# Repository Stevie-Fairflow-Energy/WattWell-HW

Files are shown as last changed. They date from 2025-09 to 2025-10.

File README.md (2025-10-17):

# Aim of the project
WattWell - An inverter, built for a lifetime. 
A home inverter, to interface battery systems and PV systems with the UK and EU electricity grids.

The WattWell must be:
- Durable
- Repairable
- Open-Source

The main goal of the project is to develop an open source inverter (Hardware and Software).  
The initial configuration of the project will be a single phase, 5 kW inverter. 

An important part of the project is to be able to work with different types of switching components (IGBT/MOSFET). Nowadays, we often see that inverters are replaced after 10 years but they keep working or some faulty inverters that are not easily repared because the design is not modular or easy to fix.

Then, the goal is to design an Open Source inverter that is modular to be easy to be fixed and flexible enough to have differents functionalities (batteries/PV/...)

The project will be divided into different "workpackages" based on the functional blocks needed to make the whole system work. These functional blocks are called "Modules", and may be split into further modules where necessary. The diagram below shows the module definitions we are currently working to. 

WattWell Block Diagram-External Interfaces - Operational drawio (3)

1. Supervisory control: development of the main control board able to get the measurements, generate references, ... This board embeds the main mcu.
2. Inverter Board
3. DC/DC converter: Able to take a variable DC input (48V +/- 20%) and output a stable DC output controllable between 360 V and 500 V.
4. DC Link: A DC link capable of self-protection
5. A DC filter for smooth input/output
6. DC Protections for over-current and over-voltage protection
7. DC connections for physically connecting the DC source to WattWell
8.  AC filter for smooth sine wave input/output
9. AC protection for over-current and over-voltage protection. Required for compatibility with grid codes.
10. Connections for phsyically conecting the external electrical system to WattWell
11. Human Machine Interface (HMI) to act as the interface between the user and the supervisory control

For the Inverter board, two sub-modules are assumed:
1. Control and Driver board: interface between the supervisory control board and power switch (IGBT's/Mosfet's). The driver board needs to generate the PWM signals based on a reference from the supervisor.
2. Power circuit: power circuit of the inverter

# Expected functionalities

- Being able (and allowed) to be connected to the European grid
- MPPT for solar panels (with DC/DC)
- Battery connection
- Communication capabilities (serial,...)
- Working in islanding mode (offgrid)

# 1. Supervisory control board:

For the supervisory control, the firmware on the main mcu should have (main mcu based on STM32G434):

1. Low level drivers
2. Basics functionalities (bootloader, debug uart, pll,...)
3. Advanced functionalities (power management, MPPT, state machine)

The main control board will be able to measure:
1.  3AC voltages (max 400V) - ADC min 14bits
2.  2DC voltages (max 1500V) -ADC min 14bits
3.  4AC/DC current measurement - ADC min 14bits
4.  Temperature measurement

The main control board will have the following interface:
1.  2X UART(1X to RS485; 1X to USB)
2.  1xSPI
3.  2xI2C
4.  1xCAN
5.  6X PWM's
6.  6X DO's
7.  6X DI's
8.  6X AI'S (temp from IGBT/Mos)

Other functions:
1.  Debug LED
2.  RTC (supercap based)
3.  Additionnal ROM (TBD)
4.  Watchdog
5.  Power supply for IGBT's/Mosfets

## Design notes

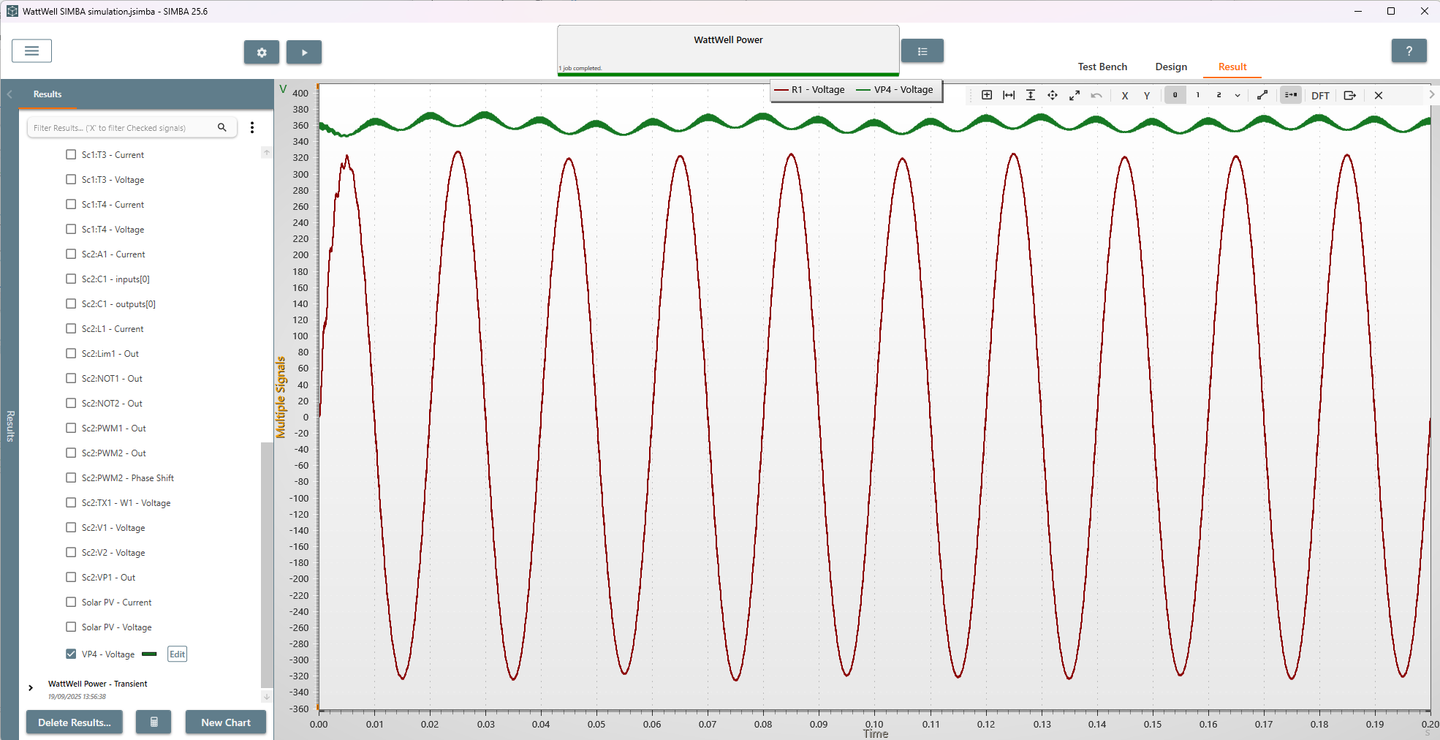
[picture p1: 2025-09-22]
WattWell-Simulations/Screenshots/Screenshot 2025-09-19 140105.png

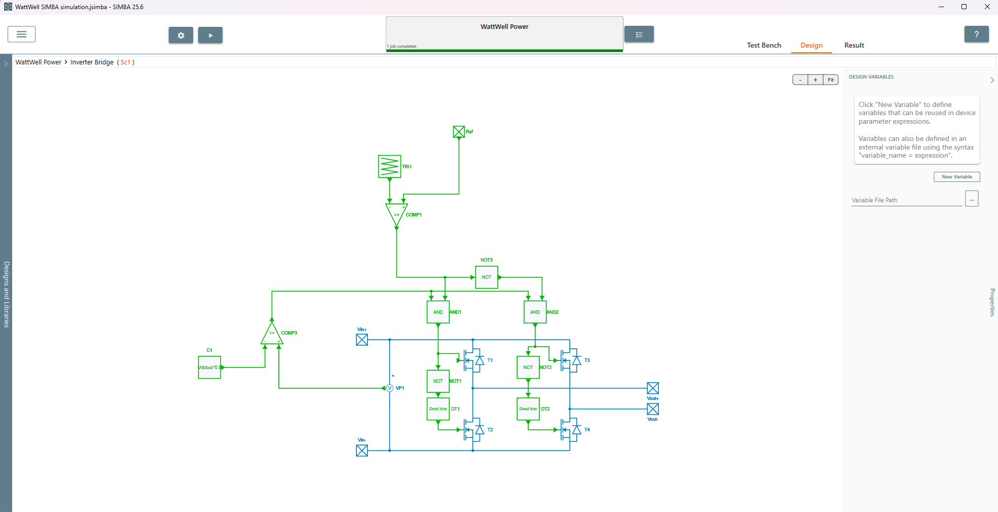
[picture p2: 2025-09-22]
WattWell-Simulations/Screenshots/Screenshot 2025-09-19 140051.png

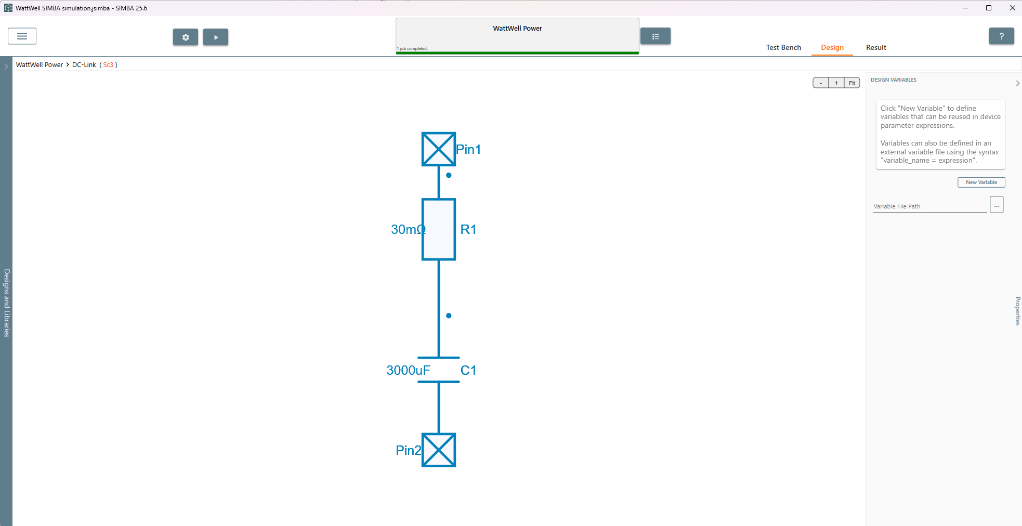
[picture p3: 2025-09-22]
WattWell-Simulations/Screenshots/Screenshot 2025-09-19 140012.png

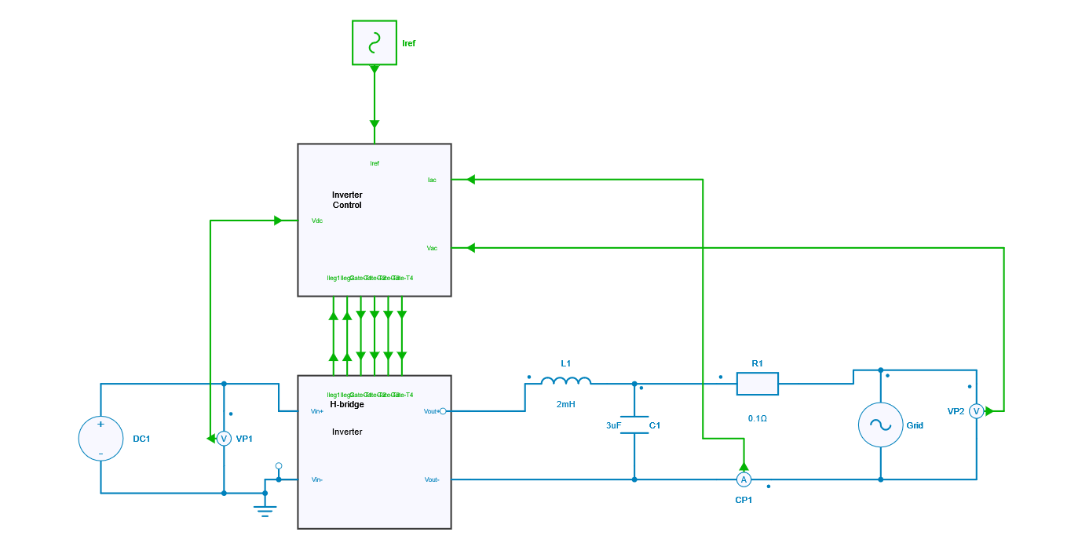
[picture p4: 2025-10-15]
WattWell-Simulations/Screenshots/Screenshot 2025-10-15 145040.png

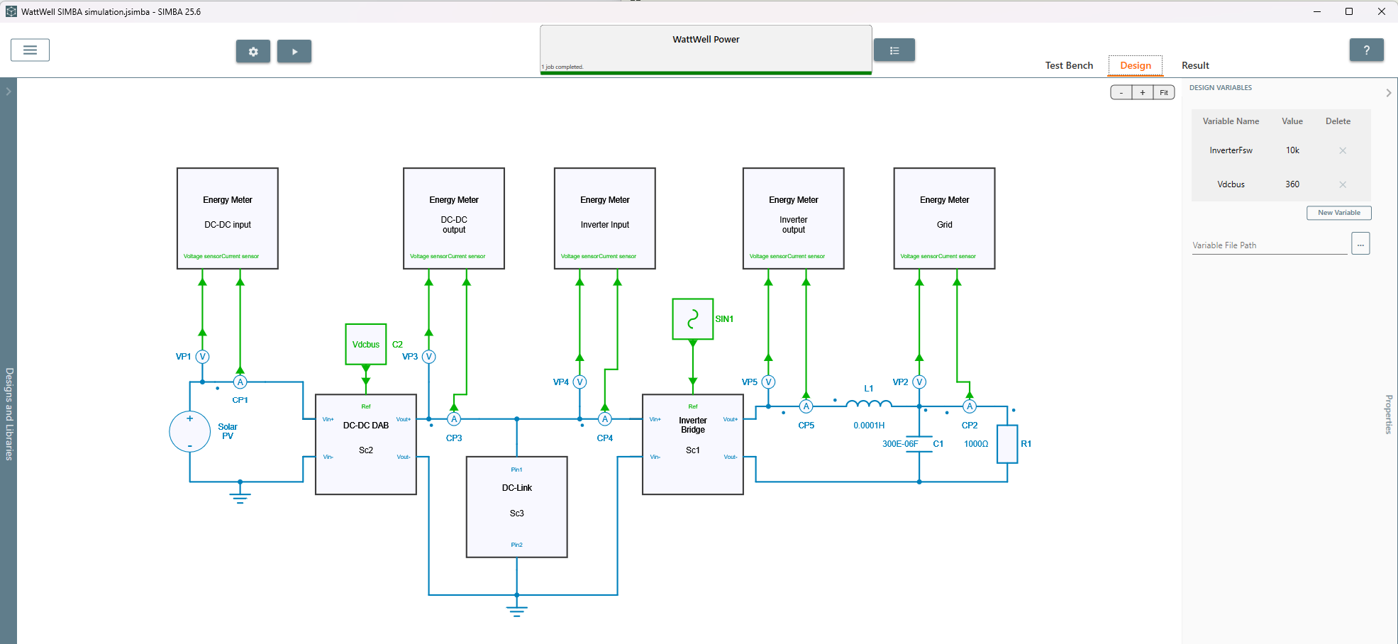
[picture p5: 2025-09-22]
WattWell-Simulations/Screenshots/Screenshot 2025-09-19 135838.png

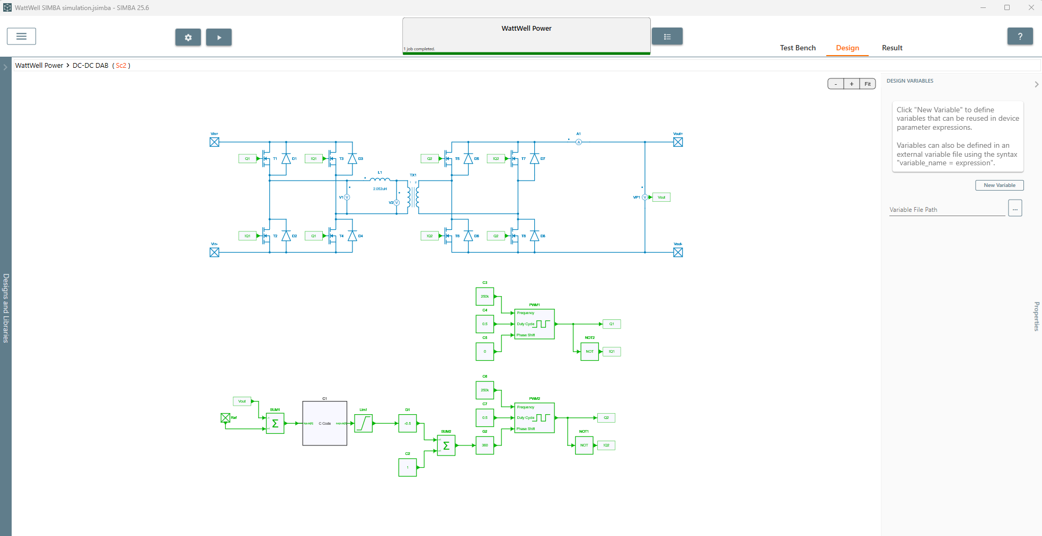
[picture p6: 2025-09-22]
WattWell-Simulations/Screenshots/Screenshot 2025-09-19 135950.png

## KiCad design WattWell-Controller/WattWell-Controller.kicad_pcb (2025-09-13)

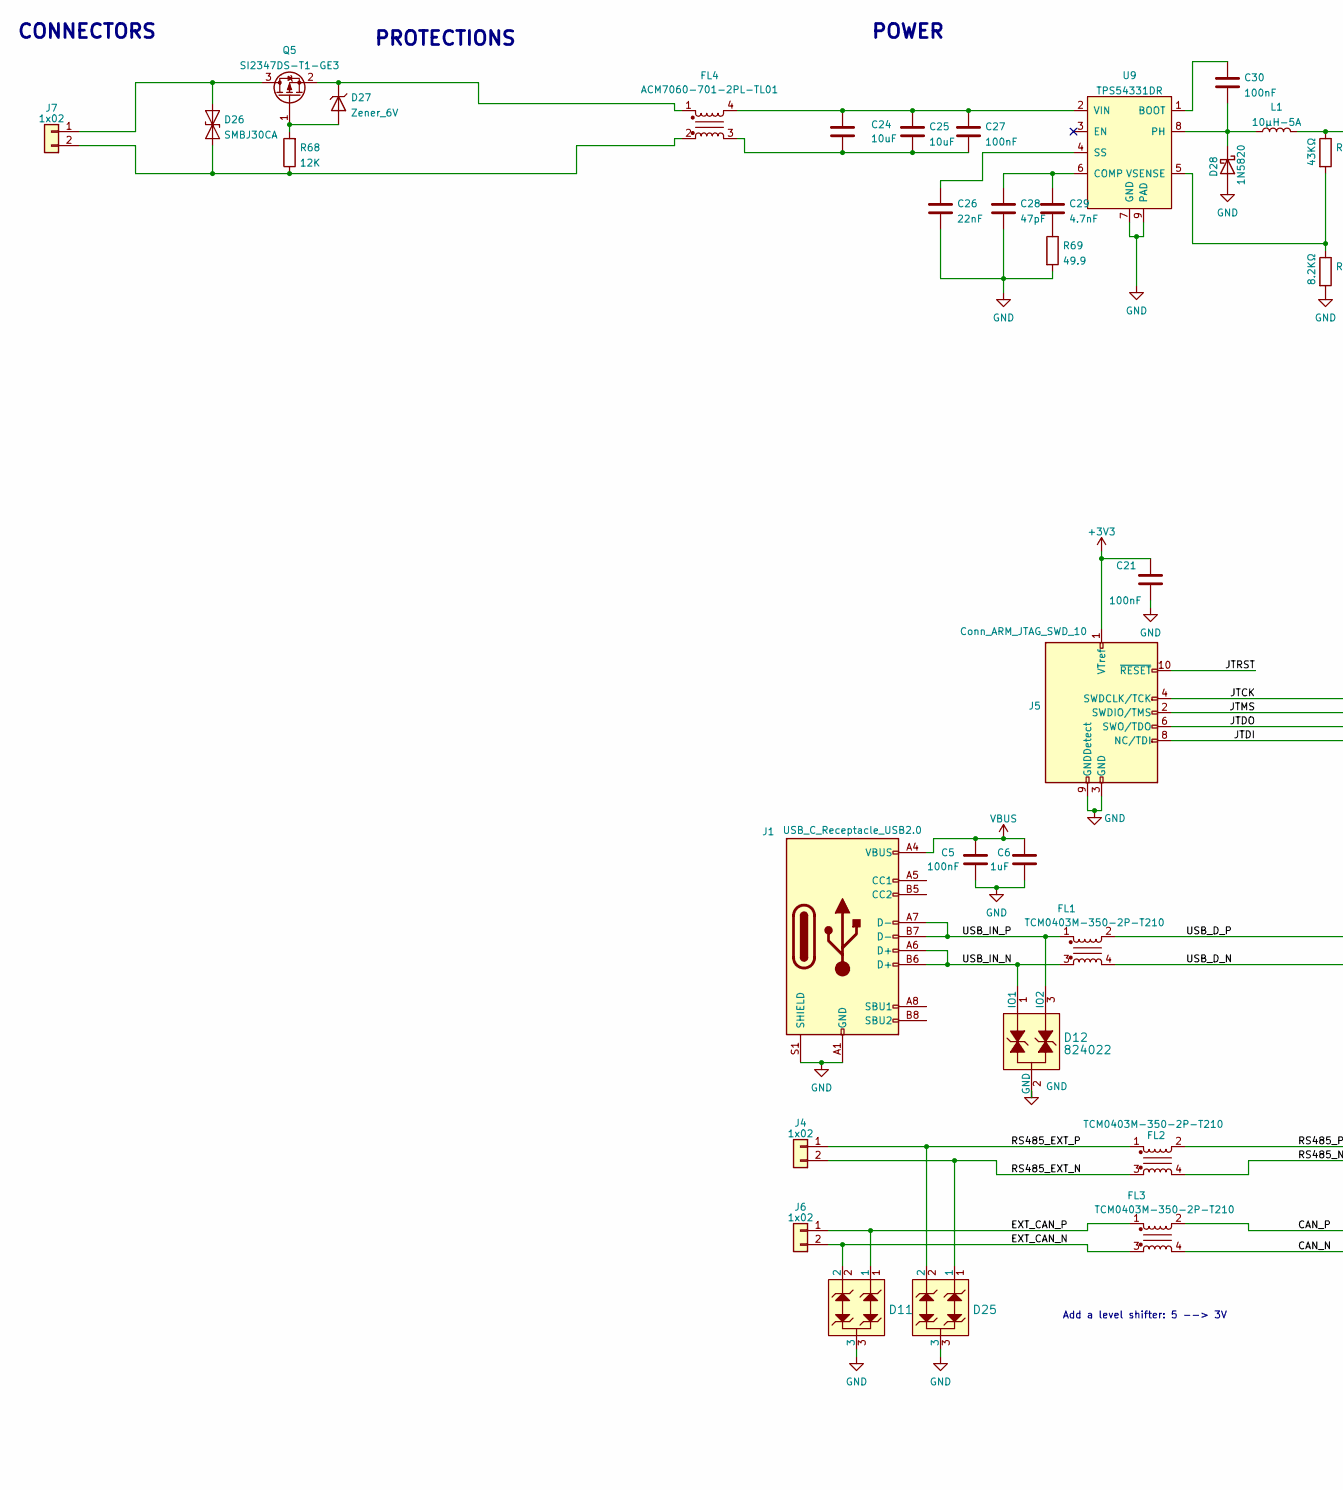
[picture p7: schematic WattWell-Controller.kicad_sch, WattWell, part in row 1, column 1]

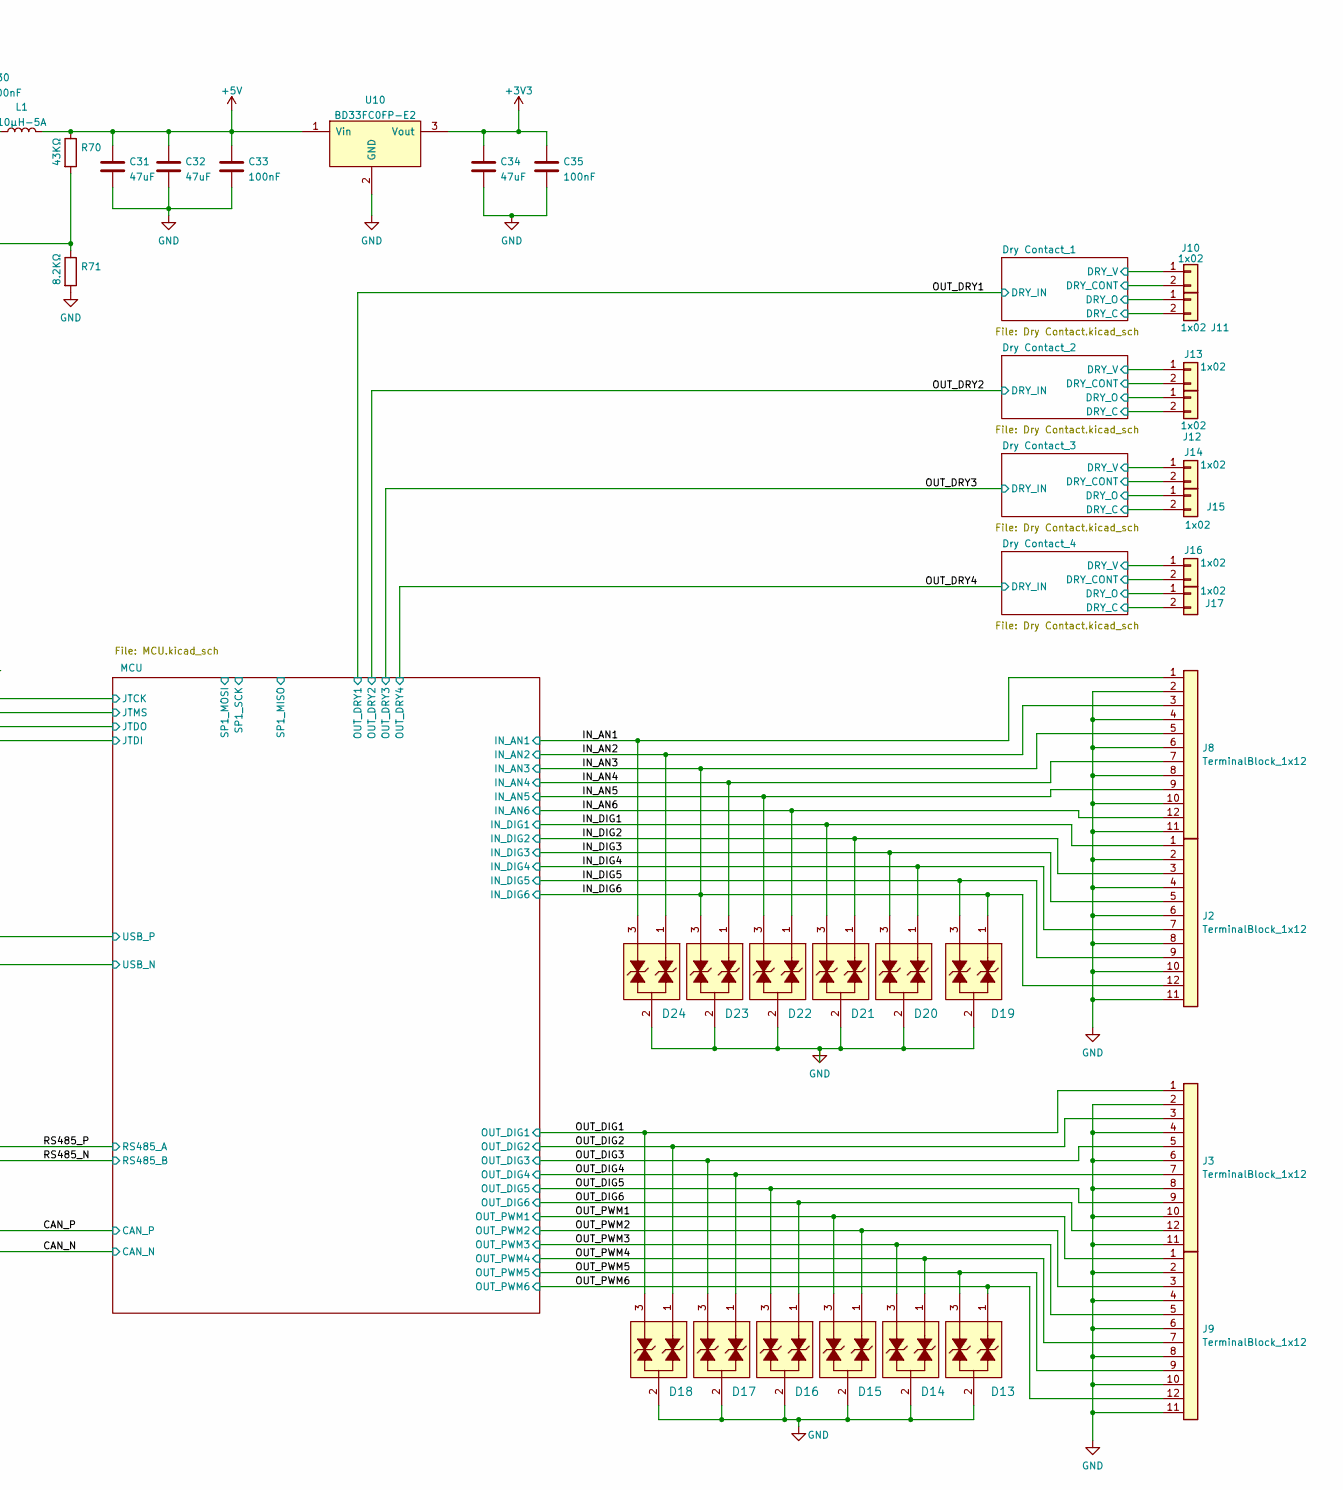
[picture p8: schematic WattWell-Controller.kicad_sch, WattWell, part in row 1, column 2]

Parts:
C5, C21, C27, C30, C33, C35: 100nF; C_0603_1608Metric; Tolerance 10%; Voltage 50V; MPN CL10B104KB8NNNC
C6: 1uF; C_0603_1608Metric; Tolerance 10%; Voltage 25V; MPN CL10B105KA8NNNC
C24, C25: 10uF; C_1206_3216Metric; Tolerance 20%; Voltage 50V; MPN GRT31CR61H106ME01L
C26: 22nF; C_0603_1608Metric; Tolerance 10%; Voltage 50V; MPN CL10B223KB8WPNC
C28: 47pF; C_0603_1608Metric; Tolerance 10%; Voltage 50V; MPN 885012006055
C29: 4.7nF; C_0603_1608Metric; Tolerance 10%; Voltage 50V; MPN CL10B472KB8NNNC
C31, C32, C34: 47uF; C_1206_3216Metric; Tolerance 10%; Voltage 10V; MPN GRT31CR61A476KE13L
D11, D25: TVS_2-Channel-7V; SOT-23; MPN CDSOT23-SM712
D12: 824022; SOT-23; MPN 824022
D13, D14, D15, D16, D17, D18, D19, D20, D21, D22, D23, D24: PESD3V3L2BT; SOT-23; MPN PESD3V3L2BT,215
D26: SMBJ30CA; D_SMB; MPN SMBJ30CA
D27: Zener_6V; D_SOD-123; Voltage 6V; MPN MMSZ5233B-E3-08
D28: 1N5820; D_DO-201AD_P15.24mm_Horizontal
FL1, FL2, FL3: TCM0403M-350-2P-T210; Choke_TDK_TCM0403M-350-2P-T210; Manufacturer Part Number TCM0403M-350-2P-T210
FL4: ACM7060-701-2PL-TL01; ChokeSMD_ACM7060; MPN ACM7060-701-2PL-TL01
J1: USB_C_Receptacle_USB2.0; USB_C_Receptacle_GCT_USB4105-xx-A_16P_TopMnt_Horizontal; MPN USB4105-GF-A-120
J2, J3, J8, J9: TerminalBlock_1x12; TerminalBlock_Phoenix_MKDS-3-12-5.08_1x12_P5.08mm_Horizontal; MPN 1795763
J4, J6, J7, J10, J11, J12, J13, J14, J15, J16, J17: 1x02; WURTH-691312510002; MPN 691312510002
J5: Conn_ARM_JTAG_SWD_10; PinHeader_2x05_P2.54mm_Vertical_SMD; MPN FTSH-105-01-L-DV-K
L1: 10μH-5A; Inductor_Wurth_XHMI-6060; MPN 74439346100
Q5: SI2347DS-T1-GE3; SOT-23; MPN SI2347DS-T1-GE3
R68: 12K; R_0603_1608Metric; MPN RT0603FRE0712KL
R69: 49.9; R_0603_1608Metric; Tolerance 1%; MPN TNPW020149R9BEED
R70: 43KΩ; R_0603_1608Metric; Tolerance 1%; MPN RC0603FR-0743KL
R71: 8.2KΩ; R_0603_1608Metric; Tolerance 1%; MPN ERJ-3EKF8201V
U9: TPS54331DR; SOIC-8-1EP_3.9x4.9mm_P1.27mm_EP2.29x3mm_ThermalVias; MPN TPS54331DR
U10: BD33FC0FP-E2; TO-252-2; MPN BD33FC0FP-E2

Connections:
+3V3: C21.1, C34.1, C35.1, J5.1 (VTref), U10.3 (Vout); also elsewhere on the board
+5V: C31.1, C32.1, C33.1, L1.2, R70.1, U10.1 (Vin); also elsewhere on the board
/CAN_N: FL3.4; also elsewhere on the board
/CAN_P: FL3.2; also elsewhere on the board
/Dry Contact_1/DRY1_C: J11.2; also elsewhere on the board
/Dry Contact_1/DRY1_O: J11.1; also elsewhere on the board
/Dry Contact_1/DRY_CONT: J10.2; also elsewhere on the board
/Dry Contact_1/DRY_V: J10.1; also elsewhere on the board
/Dry Contact_2/DRY1_C: J12.2; also elsewhere on the board
/Dry Contact_2/DRY1_O: J12.1; also elsewhere on the board
/Dry Contact_2/DRY_CONT: J13.2; also elsewhere on the board
/Dry Contact_2/DRY_V: J13.1; also elsewhere on the board
/Dry Contact_3/DRY1_C: J15.2; also elsewhere on the board
/Dry Contact_3/DRY1_O: J15.1; also elsewhere on the board
/Dry Contact_3/DRY_CONT: J14.2; also elsewhere on the board
/Dry Contact_3/DRY_V: J14.1; also elsewhere on the board
/Dry Contact_4/DRY1_C: J17.2; also elsewhere on the board
/Dry Contact_4/DRY1_O: J17.1; also elsewhere on the board
/Dry Contact_4/DRY_CONT: J16.2; also elsewhere on the board
/Dry Contact_4/DRY_V: J16.1; also elsewhere on the board
/EXT_CAN_N: D11.2, FL3.3, J6.2
/EXT_CAN_P: D11.1, FL3.1, J6.1
/IN_AN1: D24.3, J8.1; also elsewhere on the board
/IN_AN2: D24.1, J8.3; also elsewhere on the board
/IN_AN3: D19.1, D23.3, J2.12 (Pin_8), J8.5; also elsewhere on the board
/IN_AN4: D23.1, J8.7 (Pin_10); also elsewhere on the board
/IN_AN5: D22.3, J8.9 (Pin_12); also elsewhere on the board
/IN_AN6: D22.1, J8.12 (Pin_8); also elsewhere on the board
/IN_DIG1: D21.3, J2.1; also elsewhere on the board
/IN_DIG2: D21.1, J2.3; also elsewhere on the board
/IN_DIG3: D20.3, J2.5; also elsewhere on the board
/IN_DIG4: D20.1, J2.7 (Pin_10); also elsewhere on the board
/IN_DIG5: D19.3, J2.9 (Pin_12); also elsewhere on the board
/JTCK: J5.4 (SWDCLK/TCK); also elsewhere on the board
/JTDI: J5.8 (NC/TDI); also elsewhere on the board
/JTDO: J5.6 (SWO/TDO); also elsewhere on the board
/JTMS: J5.2 (SWDIO/TMS); also elsewhere on the board
/JTRST: J5.10 (~RESET)
/OUT_DIG1: D18.3, J3.1; also elsewhere on the board
/OUT_DIG2: D18.1, J3.3; also elsewhere on the board
/OUT_DIG3: D17.3, J3.5; also elsewhere on the board
/OUT_DIG4: D17.1, J3.7 (Pin_10); also elsewhere on the board
/OUT_DIG5: D16.3, J3.9 (Pin_12); also elsewhere on the board
/OUT_DIG6: D16.1, J3.12 (Pin_8); also elsewhere on the board
/OUT_PWM1: D15.3, J9.1; also elsewhere on the board
/OUT_PWM2: D15.1, J9.3; also elsewhere on the board
/OUT_PWM3: D14.3, J9.5; also elsewhere on the board
/OUT_PWM4: D14.1, J9.7 (Pin_10); also elsewhere on the board
/OUT_PWM5: D13.3, J9.9 (Pin_12); also elsewhere on the board
/OUT_PWM6: D13.1, J9.12 (Pin_8); also elsewhere on the board
/RS485_EXT_N: D25.1, FL2.3, J4.2
/RS485_EXT_P: D25.2, FL2.1, J4.1
/RS485_N: FL2.4; also elsewhere on the board
/RS485_P: FL2.2; also elsewhere on the board
/USB_D_N: FL1.4; also elsewhere on the board
/USB_D_P: FL1.2; also elsewhere on the board
/USB_IN_N: D12.1 (IO1), FL1.3, J1.A6 (D+), J1.B6 (D+)
/USB_IN_P: D12.3 (IO2), FL1.1, J1.A7 (D-), J1.B7 (D-)
GND: C5.2, C6.2, C21.2, C26.2, C28.2, C31.2, C32.2, C33.2, C34.2, C35.2, D11.3, D12.2 (GND), D13.2, D14.2, D15.2, D16.2, D17.2, D18.2, D19.2, D20.2, D21.2, D22.2, D23.2, D24.2, D25.3, D28.2 (A), J1.A1 (GND), J1.A12 (GND), J1.B1 (GND), J1.B12 (GND), J1.S1 (SHIELD), J2.2, J2.4, J2.6, J2.8 (Pin_11), J2.10 (Pin_13), J2.11 (Pin_7), J3.2, J3.4, J3.6, J3.8 (Pin_11), J3.10 (Pin_13), J3.11 (Pin_7), J5.3 (GND), J5.5 (GND), J5.9 (GNDDetect), J8.2, J8.4, J8.6, J8.8 (Pin_11), J8.10 (Pin_13), J8.11 (Pin_7), J9.2, J9.4, J9.6, J9.8 (Pin_11), J9.10 (Pin_13), J9.11 (Pin_7), R69.2, R71.2, U9.7 (GND), U9.9 (PAD), U10.2 (GND); also elsewhere on the board
unnamed: C24.2, C25.2, C27.2, FL4.3
unnamed: C29.2, R69.1
unnamed: D26.1 (A1), FL4.2, J7.2, R68.1
unnamed: D26.2 (A2), J7.1, Q5.3 (D)
unnamed: D27.2 (A), Q5.1 (G), R68.2
unnamed: D27.1 (K), FL4.1, Q5.2 (S)
unnamed: C30.2, D28.1 (K), L1.1, U9.8 (PH)
unnamed: C30.1, U9.1 (BOOT)
unnamed: C28.1, C29.1, U9.6 (COMP)
unnamed: C26.1, U9.4 (SS)
unnamed: C24.1, C25.1, C27.1, FL4.4, U9.2 (VIN)
unnamed: R70.2, R71.1, U9.5 (VSENSE)
VBUS: C5.1, C6.1, J1.A4 (VBUS), J1.A9 (VBUS), J1.B4 (VBUS), J1.B9 (VBUS); also elsewhere on the board

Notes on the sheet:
CONNECTORS
POWER
Add a level shifter: 5 --> 3V
PROTECTIONS

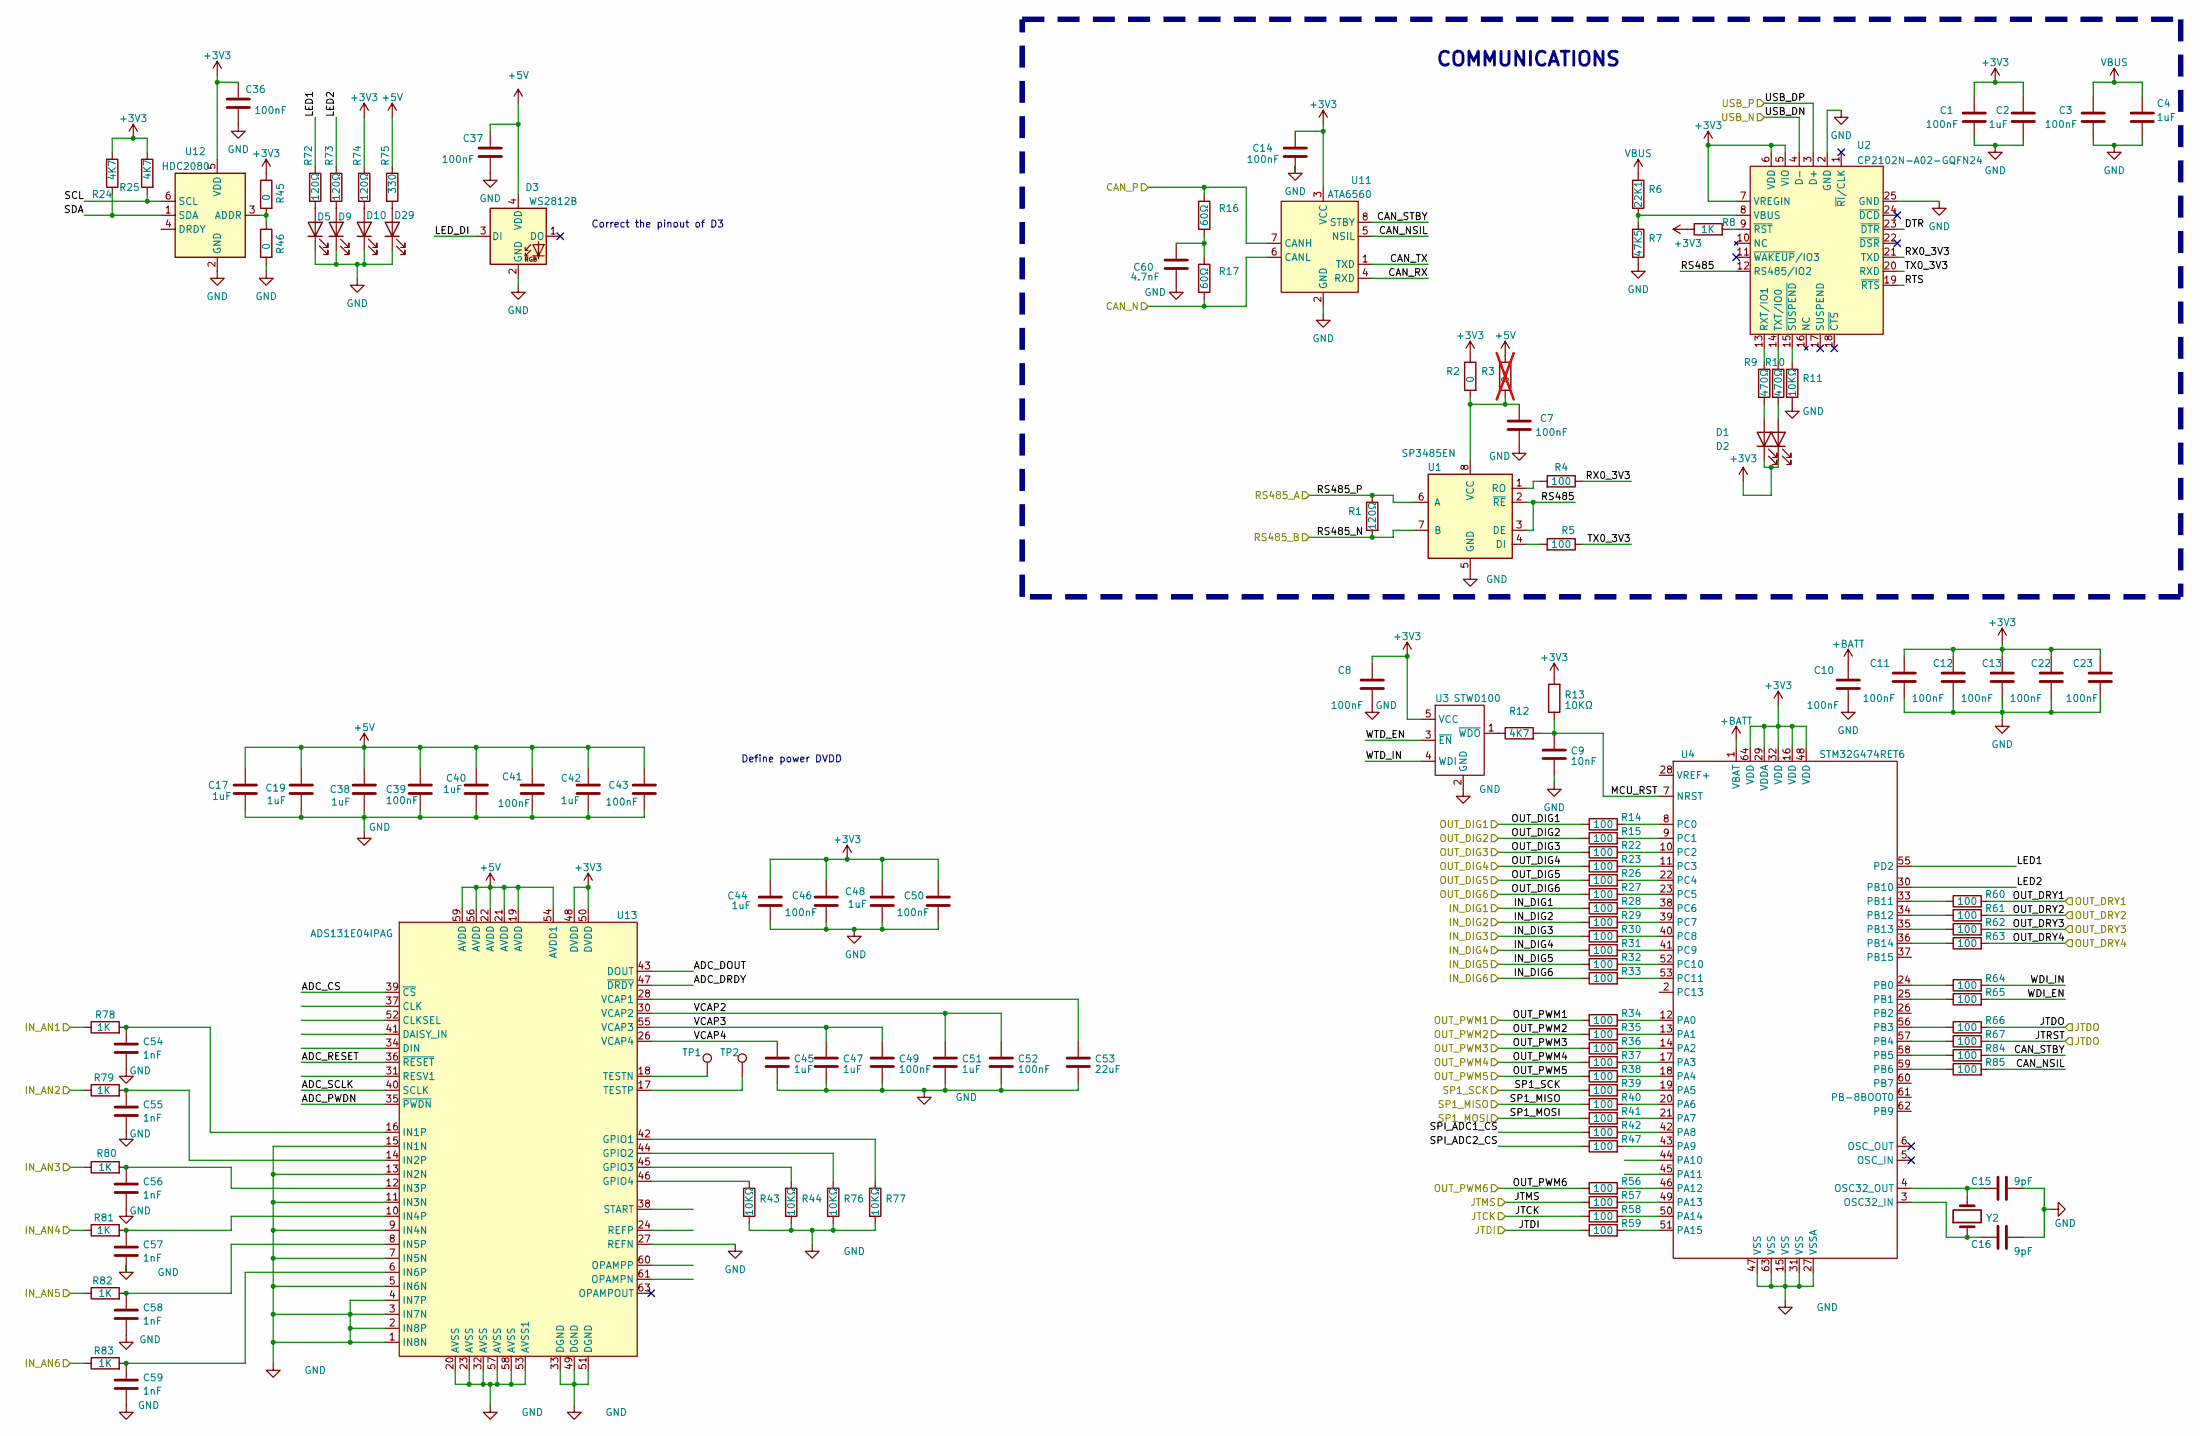
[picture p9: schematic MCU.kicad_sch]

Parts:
C1, C3, C7, C8, C10, C11, C12, C13, C14, C22, C23, C36, C37, C39, C41, C43, C46, C49, C50, C52: 100nF; C_0603_1608Metric; Tolerance 10%; Voltage 50V; MPN CL10B104KB8NNNC
C2, C4, C17, C19, C38, C40, C42, C44, C45, C47, C48, C51: 1uF; C_0603_1608Metric; Tolerance 10%; Voltage 25V; MPN CL10B105KA8NNNC
C9: 10nF; C_0603_1608Metric; Tolerance 10%; Voltage 50V; MPN CL10B103KB8NNNC
C15, C16: 9pF; C_0603_1608Metric; Tolerance 0.5%; Voltage 50VDC; MPN 0603N9R0D500CT
C53: 22uF; C_1206_3216Metric; Tolerance 20%; Voltage 10V; MPN CL31B226MPHNNNE
C54, C55, C56, C57, C58, C59: 1nF; C_0603_1608Metric; Tolerance 10%; Voltage 50V; MPN CL10B102KB8NNNC
C60: 4.7nF; C_0603_1608Metric; Tolerance 10%; Voltage 50V; MPN CL10B472KB8NNNC
D1, D2: LED_Small; LED_0603_1608Metric; MPN 150060RS55040
D3: WS2812B; LED_WS2812B_PLCC4_5.0x5.0mm_P3.2mm; Manufacturer Part Number 4684
D5, D9, D10, D29: 150060RS55040; LED_0603_1608Metric; MPN 150060RS55040
R1, R72, R73, R74: 120Ω; R_0603_1608Metric; Tolerance 5%; MPN CR0603-FX-1200ELF
R2, R45, R46: 0; R_0603_1608Metric; MPN RC0603JR-070RL
R3: 0; R_0603_1608Metric; MPN RC0603JR-070RL; not fitted
R4, R5, R14, R15, R22, R23, R26, R27, R28, R29, R30, R31, R32, R33, R34, R35, R36, R37, R38, R39, R40, R41, R42, R47, R56, R57, R58, R59, R60, R61, R62, R63, R64, R65, R66, R67, R84, R85: 100; R_0603_1608Metric; Tolerance 1%; MPN RC0603FR-07100RL
R6: 22K1; R_0603_1608Metric; MPN CR0603-FX-2212ELF
R7: 47K5; R_0603_1608Metric; MPN RT0603DRE0747K5L
R8, R78, R79, R80, R81, R82, R83: 1K; R_0603_1608Metric; Tolerance 1%; MPN RC0603FR-071KL
R9, R10: 470Ω; R_0603_1608Metric; Tolerance 5%; MPN CRCW0603470RJNEBC
R11, R13, R43, R44, R76, R77: 10KΩ; R_0603_1608Metric; Tolerance 1%; MPN ERJ-3EKF1002V
R12, R24, R25: 4K7; R_0603_1608Metric; Tolerance 1%; MPN CRGH0603F4K7
R16, R17: 60Ω; R_0603_1608Metric; Tolerance 1%; MPN CPF0603F60R4C1
R75: 330; R_0603_1608Metric; Tolerance 1%; MPN AF0402JR-07330RL
TP1, TP2: TestPoint_1.5mm; TestPoint_Pad_D1.5mm
U1: SP3485EN; SOIC-8_3.9x4.9mm_P1.27mm; Manufacturer Part Number MAX3072EASA+
U2: CP2102N-A02-GQFN24; QFN-24-1EP_4x4mm_P0.5mm_EP2.6x2.6mm; MPN CP2102N-A02-GQFN24
U3: STWD100; SOT-23-5; Manufacturer Part Number STWD100YNWWY3F
U4: LQFP-64_10x10mm_P0.5mm; Manufacturer Part Number STM32G474RET6
U11: ATA6560; SOIC-8_3.9x4.9mm_P1.27mm; Manufacturer Part Number ATA6560-GAQW-N
U12: HDC2080; Texas_PWSON-N6; MPN HDC2080DMBT
U13: LQFP-64_10x10mm_P0.5mm; MPN ADS131E04IPAG
Y2: Crystal; Oscillator_SMD_ECS_2520MV-xxx-xx-4Pin_2.5x2.0mm; MPN ECS-.327-9-34QCS-TR9

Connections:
+3V3: C1.1, C2.1, C8.1, C11.1, C12.1, C13.1, C14.1, C22.1, C23.1, C36.1, C44.1, C46.1, C48.1, C50.1, D1.2 (K), D2.2 (K), R2.1, R8.1, R13.2, R24.2, R25.1, R45.1, R74.1, U2.5 (VIO), U2.6 (VDD), U2.7 (VREGIN), U3.5 (VCC), U4.16 (VDD), U4.29 (VDDA), U4.32 (VDD), U4.48 (VDD), U4.64 (VDD), U11.3 (VCC), U12.5 (VDD), U13.48 (DVDD), U13.50 (DVDD); also elsewhere on the board
+5V: C17.1, C19.1, C37.1, C38.1, C39.1, C40.1, C41.1, C42.1, C43.1, D3.4 (VDD), R3.1, R75.1, U13.19 (AVDD), U13.21 (AVDD), U13.22 (AVDD), U13.54 (AVDD1), U13.56 (AVDD), U13.59 (AVDD); also elsewhere on the board
+BATT: C10.1, U4.1 (VBAT)
/CAN_N: R17.2, U11.6 (CANL); also elsewhere on the board
/CAN_P: R16.1, U11.7 (CANH); also elsewhere on the board
/IN_AN1: R78.1; also elsewhere on the board
/IN_AN2: R79.1; also elsewhere on the board
/IN_AN3: R33.1, R80.1; also elsewhere on the board
/IN_AN4: R81.1; also elsewhere on the board
/IN_AN5: R82.1; also elsewhere on the board
/IN_AN6: R83.1; also elsewhere on the board
/IN_DIG1: R28.1; also elsewhere on the board
/IN_DIG2: R29.1; also elsewhere on the board
/IN_DIG3: R30.1; also elsewhere on the board
/IN_DIG4: R31.1; also elsewhere on the board
/IN_DIG5: R32.1; also elsewhere on the board
/JTCK: R58.1; also elsewhere on the board
/JTDI: R59.1; also elsewhere on the board
/JTDO: R66.2, R67.2; also elsewhere on the board
/JTMS: R57.1; also elsewhere on the board
/MCU/ADC_CS: U13.39 (~CS)
/MCU/ADC_DOUT: U13.43 (DOUT)
/MCU/ADC_DRDY: U13.47 (~DRDY)
/MCU/ADC_PWDN: U13.35 (~PWDN)
/MCU/ADC_RESET: U13.36 (~RESET)
/MCU/ADC_SCLK: U13.40 (SCLK)
/MCU/CAN_NSIL: R85.2, U11.5 (NSIL)
/MCU/CAN_RX: U11.4 (RXD)
/MCU/CAN_STBY: R84.2, U11.8 (STBY)
/MCU/CAN_TX: U11.1 (TXD)
/MCU/DTR: U2.23 (~DTR)
/MCU/LED1: R72.1, U4.55 (PD2)
/MCU/LED2: R73.1, U4.30 (PB10)
/MCU/LED_DI: D3.3 (DI)
/MCU/MCU_RST: C9.2, R12.2, R13.1, U4.7 (NRST)
/MCU/RS485: U1.2 (~RE), U1.3 (DE), U2.12 (RS485/IO2)
/MCU/RTS: U2.19 (~RTS)
/MCU/RX0_3V3: R4.1, U2.21 (TXD)
/MCU/SCL: R25.2, U12.6 (SCL)
/MCU/SDA: R24.1, U12.1 (SDA)
/MCU/SP1_MISO: R40.1
/MCU/SP1_MOSI: R41.1
/MCU/SP1_SCK: R39.1
/MCU/SPI_ADC1_CS: R42.1
/MCU/SPI_ADC2_CS: R47.1
/MCU/TX0_3V3: R5.1, U2.20 (RXD)
/MCU/VCAP2: C51.1, C52.1, U13.30 (VCAP2)
/MCU/VCAP3: C47.1, C49.1, U13.55 (VCAP3)
/MCU/VCAP4: C45.1, U13.26 (VCAP4)
/MCU/WDI_EN: R65.2
/MCU/WDI_IN: R64.2
/MCU/WTD_EN: U3.3 (~EN)
/MCU/WTD_IN: U3.4 (WDI)
/OUT_DIG1: R14.1; also elsewhere on the board
/OUT_DIG2: R15.1; also elsewhere on the board
/OUT_DIG3: R22.1; also elsewhere on the board
/OUT_DIG4: R23.1; also elsewhere on the board
/OUT_DIG5: R26.1; also elsewhere on the board
/OUT_DIG6: R27.1; also elsewhere on the board
/OUT_DRY1: R60.2; also elsewhere on the board
/OUT_DRY2: R61.2; also elsewhere on the board
/OUT_DRY3: R62.2; also elsewhere on the board
/OUT_DRY4: R63.2; also elsewhere on the board
/OUT_PWM1: R34.1; also elsewhere on the board
/OUT_PWM2: R35.1; also elsewhere on the board
/OUT_PWM3: R36.1; also elsewhere on the board
/OUT_PWM4: R37.1; also elsewhere on the board
/OUT_PWM5: R38.1; also elsewhere on the board
/OUT_PWM6: R56.1; also elsewhere on the board
/RS485_N: R1.2, U1.7 (B); also elsewhere on the board
/RS485_P: R1.1, U1.6 (A); also elsewhere on the board
/USB_D_N: U2.4 (D-); also elsewhere on the board
/USB_D_P: U2.3 (D+); also elsewhere on the board
GND: C1.2, C2.2, C3.2, C4.2, C7.2, C8.2, C9.1, C10.2, C11.2, C12.2, C13.2, C14.2, C15.2, C16.2, C17.2, C19.2, C22.2, C23.2, C36.2, C37.2, C38.2, C39.2, C40.2, C41.2, C42.2, C43.2, C44.2, C45.2, C46.2, C47.2, C48.2, C49.2, C50.2, C51.2, C52.2, C53.2, C54.2, C55.2, C56.2, C57.2, C58.2, C59.2, C60.1, D3.2 (GND), D5.2 (K), D9.2 (K), D10.2 (K), D29.2 (K), R7.2, R11.2, R43.2, R44.2, R46.2, R76.2, R77.2, U1.5 (GND), U2.2 (GND), U2.25 (GND), U3.2 (GND), U4.15 (VSS), U4.27 (VSSA), U4.31 (VSS), U4.47 (VSS), U4.63 (VSS), U11.2 (GND), U12.2 (GND), U13.1 (IN8N), U13.2 (IN8P), U13.3 (IN7N), U13.4 (IN7P), U13.5 (IN6N), U13.7 (IN5N), U13.9 (IN4N), U13.11 (IN3N), U13.13 (IN2N), U13.15 (IN1N), U13.20 (AVSS), U13.23 (AVSS), U13.27 (REFN), U13.32 (AVSS), U13.33 (DGND), U13.49 (DGND), U13.51 (DGND), U13.53 (AVSS1), U13.57 (AVSS), U13.58 (AVSS); also elsewhere on the board
unnamed: C60.2, R16.2, R17.1
unnamed: D1.1 (A), R9.2
unnamed: D2.1 (A), R10.2
unnamed: D5.1 (A), R72.2
unnamed: D9.1 (A), R73.2
unnamed: D10.1 (A), R74.2
unnamed: D29.1 (A), R75.2
unnamed: R5.2, U1.4 (DI)
unnamed: R4.2, U1.1 (RO)
unnamed: C7.1, R2.2, R3.2, U1.8 (VCC)
unnamed: R9.1, U2.13 (RXT/IO1)
unnamed: R10.1, U2.14 (TXT/IO0)
unnamed: R6.2, R7.1, U2.8 (VBUS)
unnamed: R8.2, U2.9 (~RST)
unnamed: R11.1, U2.15 (~SUSPEND)
unnamed: R12.1, U3.1 (~WDO)
unnamed: C16.1, U4.3 (OSC32_IN), Y2.1
unnamed: C15.1, U4.4 (OSC32_OUT), Y2.2
unnamed: R34.2, U4.12 (PA0)
unnamed: R35.2, U4.13 (PA1)
unnamed: R36.2, U4.14 (PA2)
unnamed: R37.2, U4.17 (PA3)
unnamed: R38.2, U4.18 (PA4)
unnamed: R39.2, U4.19 (PA5)
unnamed: R40.2, U4.20 (PA6)
unnamed: R41.2, U4.21 (PA7)
unnamed: R42.2, U4.42 (PA8)
unnamed: R47.2, U4.43 (PA9)
unnamed: R56.2, U4.46 (PA12)
unnamed: R57.2, U4.49 (PA13)
unnamed: R58.2, U4.50 (PA14)
unnamed: R59.2, U4.51 (PA15)
unnamed: R64.1, U4.24 (PB0)
unnamed: R65.1, U4.25 (PB1)
unnamed: R66.1, U4.56 (PB3)
unnamed: R67.1, U4.57 (PB4)
unnamed: R84.1, U4.58 (PB5)
unnamed: R85.1, U4.59 (PB6)
unnamed: R60.1, U4.33 (PB11)
unnamed: R61.1, U4.34 (PB12)
unnamed: R62.1, U4.35 (PB13)
unnamed: R63.1, U4.36 (PB14)
unnamed: R14.2, U4.8 (PC0)
unnamed: R15.2, U4.9 (PC1)
unnamed: R22.2, U4.10 (PC2)
unnamed: R23.2, U4.11 (PC3)
unnamed: R26.2, U4.22 (PC4)
unnamed: R27.2, U4.23 (PC5)
unnamed: R28.2, U4.38 (PC6)
unnamed: R29.2, U4.39 (PC7)
unnamed: R30.2, U4.40 (PC8)
unnamed: R31.2, U4.41 (PC9)
unnamed: R32.2, U4.52 (PC10)
unnamed: R33.2, U4.53 (PC11)
unnamed: R45.2, R46.1, U12.3 (ADDR)
unnamed: R77.1, U13.42 (GPIO1)
unnamed: R76.1, U13.44 (GPIO2)
unnamed: R44.1, U13.45 (GPIO3)
unnamed: R43.1, U13.46 (GPIO4)
unnamed: C54.1, R78.2, U13.16 (IN1P)
unnamed: C55.1, R79.2, U13.14 (IN2P)
unnamed: C56.1, R80.2, U13.12 (IN3P)
unnamed: C57.1, R81.2, U13.10 (IN4P)
unnamed: C58.1, R82.2, U13.8 (IN5P)
unnamed: C59.1, R83.2, U13.6 (IN6P)
unnamed: TP1.1, U13.18 (TESTN)
unnamed: TP2.1, U13.17 (TESTP)
unnamed: C53.1, U13.28 (VCAP1)
VBUS: C3.1, C4.1, R6.1; also elsewhere on the board

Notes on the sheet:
COMMUNICATIONS
Define power DVDD
Correct the pinout of D3

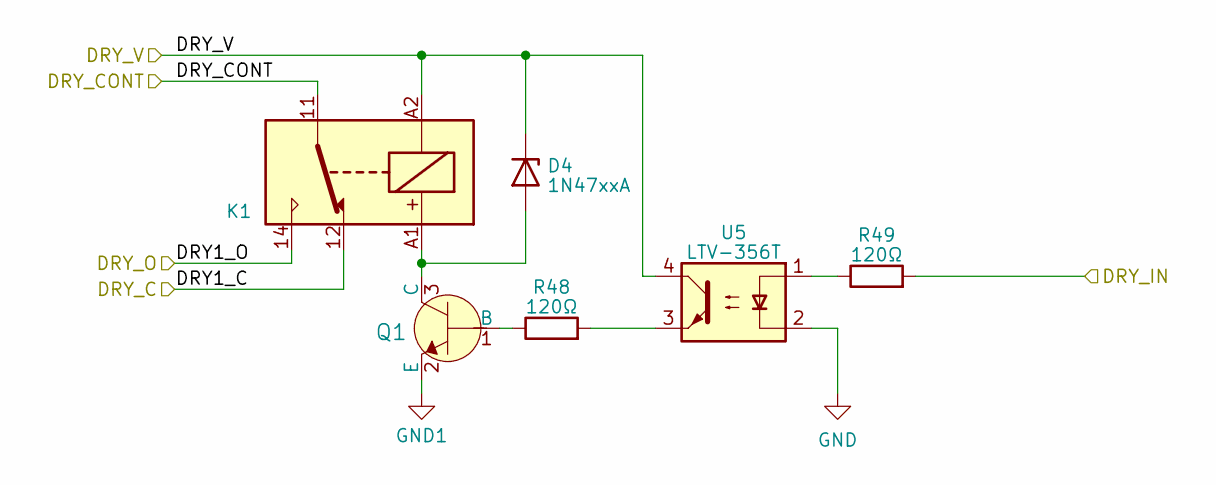
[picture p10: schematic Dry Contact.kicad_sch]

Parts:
D4: 1N47xxA; D_DO-41_SOD81_P10.16mm_Horizontal
K1: RZH3-1C4-D012; Relay_TE_RZH3-1C04-D012; Manufacturer Part Number 2-1415899-5
Q1: MMSS8050-H-TP; SOT-23; MPN MMSS8050-H-TP
R48, R49: 120Ω; R_0603_1608Metric; Tolerance 5%; MPN CR0603-FX-1200ELF
U5: LTV-356T; SO-4_4.4x3.6mm_P2.54mm

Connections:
/Dry Contact_1/DRY1_C: K1.12; also elsewhere on the board
/Dry Contact_1/DRY1_O: K1.14; also elsewhere on the board
/Dry Contact_1/DRY_CONT: K1.11; also elsewhere on the board
/Dry Contact_1/DRY_V: D4.1 (K), K1.A2, U5.4; also elsewhere on the board
/OUT_DRY1: R49.2; also elsewhere on the board
GND: U5.2; also elsewhere on the board
GND1: Q1.2 (E); also elsewhere on the board
unnamed: D4.2 (A), K1.A1, Q1.3 (C)
unnamed: Q1.1 (B), R48.1
unnamed: R48.2, U5.3
unnamed: R49.1, U5.1

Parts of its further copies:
D6, D7, D8: 1N47xxA; D_DO-41_SOD81_P10.16mm_Horizontal
K2, K3, K4: RZH3-1C4-D012; Relay_TE_RZH3-1C04-D012; Manufacturer Part Number 2-1415899-5
Q2, Q3, Q4: MMSS8050-H-TP; SOT-23; MPN MMSS8050-H-TP
R50, R51, R52, R53, R54, R55: 120Ω; R_0603_1608Metric; Tolerance 5%; MPN CR0603-FX-1200ELF
U6, U7, U8: LTV-356T; SO-4_4.4x3.6mm_P2.54mm

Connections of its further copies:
/Dry Contact_2/DRY1_C: K2.12; also elsewhere on the board
/Dry Contact_2/DRY1_O: K2.14; also elsewhere on the board
/Dry Contact_2/DRY_CONT: K2.11; also elsewhere on the board
/Dry Contact_2/DRY_V: D6.1 (K), K2.A2, U6.4; also elsewhere on the board
/Dry Contact_3/DRY1_C: K3.12; also elsewhere on the board
/Dry Contact_3/DRY1_O: K3.14; also elsewhere on the board
/Dry Contact_3/DRY_CONT: K3.11; also elsewhere on the board
/Dry Contact_3/DRY_V: D7.1 (K), K3.A2, U7.4; also elsewhere on the board
/Dry Contact_4/DRY1_C: K4.12; also elsewhere on the board
/Dry Contact_4/DRY1_O: K4.14; also elsewhere on the board
/Dry Contact_4/DRY_CONT: K4.11; also elsewhere on the board
/Dry Contact_4/DRY_V: D8.1 (K), K4.A2, U8.4; also elsewhere on the board
/OUT_DRY2: R51.2; also elsewhere on the board
/OUT_DRY3: R53.2; also elsewhere on the board
/OUT_DRY4: R55.2; also elsewhere on the board
GND: U6.2, U7.2, U8.2; also elsewhere on the board
GND1: Q2.2 (E), Q3.2 (E), Q4.2 (E); also elsewhere on the board
unnamed: D6.2 (A), K2.A1, Q2.3 (C)
unnamed: D7.2 (A), K3.A1, Q3.3 (C)
unnamed: D8.2 (A), K4.A1, Q4.3 (C)
unnamed: Q2.1 (B), R50.1
unnamed: Q3.1 (B), R52.1
unnamed: Q4.1 (B), R54.1
unnamed: R50.2, U6.3
unnamed: R51.1, U6.1
unnamed: R52.2, U7.3
unnamed: R53.1, U7.1
unnamed: R54.2, U8.3
unnamed: R55.1, U8.1

Board: 2 copper layers, 215 parts (0 on the bottom side), 174 nets, no tracks yet.

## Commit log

2025-01-14 Component placement continued
    [WattWell-Controller.kicad_pcb]
2025-05-28 Layout continued. Placement
    [Dry Contact.kicad_sch, MCU.kicad_sch, WattWell-Controller.kicad_pcb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]
2025-09-11 Placement continued Changed the order of Terminal block connectors
    [MCU.kicad_sch, WattWell-Controller.kicad_pcb]
2025-09-12 Placement continued
    [WattWell-Controller.kicad_pcb]
2025-09-13 Placement continued ADC powered to 5V and 3.3
    [MCU.kicad_sch, WattWell-Controller.kicad_pcb, WattWell-Controller.kicad_sch]
2025-09-13 Schematic and placement continued
    [MCU.kicad_sch, WattWell-Controller.kicad_pcb]
2025-09-17 First basic simulation of inverter power circuit and simple control
2025-09-22 Differential voltage probes for correct energy metering.
2025-09-30 Added instantaneous current protection
    Instantaneous current protection implemented within the H bridge module.
2025-09-30 Added a sample time to stop inconsistent graphing
2025-09-30 Simple thermal model setup for MOSFETs
2025-10-14 SIMBA Simulation improvements - inverter control
    Simple current control with feed-forward voltage working in simulation.
2025-10-14 Minor simulation tweaks
    Minor tweaks to try current limiting.
    Added datasheet of relevant current transformer for fast protection.
2025-10-16 PID control added for current mode
    PID control added for current mode.
    Attempts to get AC sweep working, but unsuccessful.
2025-10-17 Working simple voltage PID control
    Working simple PID control, note that the response is not super smooth!
2025-10-17 Added limiter - more stable voltage control
